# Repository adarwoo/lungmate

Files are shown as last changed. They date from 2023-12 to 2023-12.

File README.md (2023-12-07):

# Dust Extractor Manager for woodworking machinary

Guillaume Arreckx (United Kingdom)

**This was automatically translated from French**

This project should delight carpentry workshop owners who use
woodworking machinary with a chip dust extractor. Thanks to the
'LungMate', you no longer need to worry about the dust extractor,
because it turns on automatically each time you start one of the
machines in the workshop, then turns off once the work is finished. The
assembly is discreet and is placed directly in the workshop's electrical
panel. It precisely measures machine currents via a contactless Hall
effect sensor and transmits the results over a serial interface. It also
allows you to control the dust extractor manually with a simple push
button.

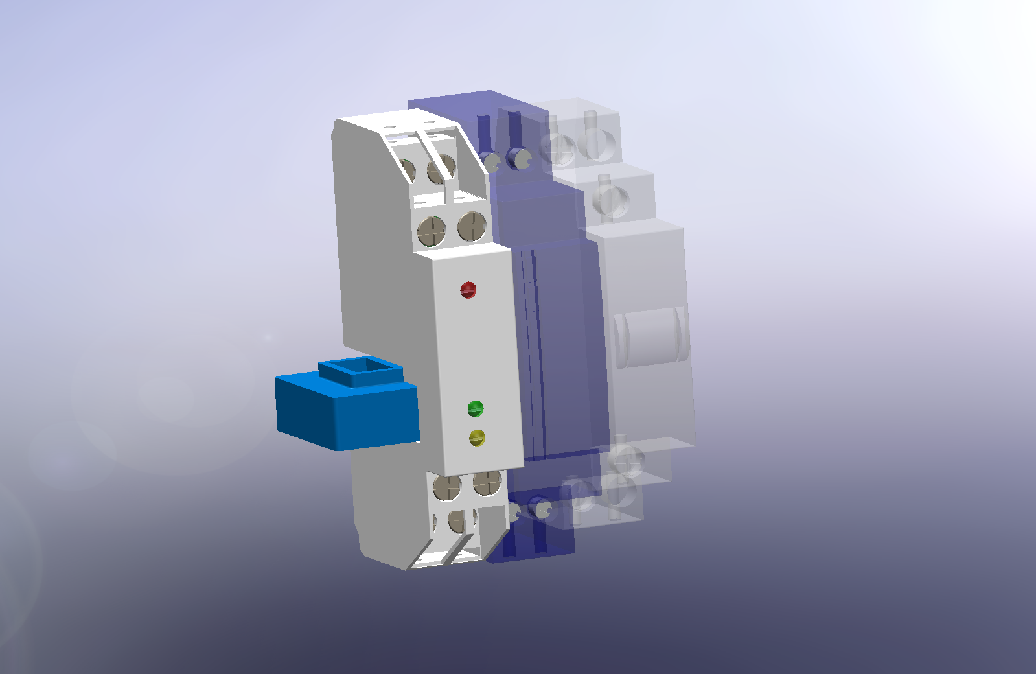
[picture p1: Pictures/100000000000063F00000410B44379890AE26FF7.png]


Woodworking machines generate enormous quantities of sawdust and the use
of a chip dust extractor is essential in a workshop. The paradox is that
these dust extractors generate a lot of fine and harmful dust in the
air. They are also noisy and power hungry. They should therefore only be
turned on when necessary. LungMate turns on the chip vacuum each time
one of the woodworking machines starts, then turns it off a few seconds
after the last machine stops, to allow the evacuation of the chips
remaining in the pipes.

Ignition is also slightly delayed; Woodworking machines, which mostly
use induction motors, require a very high starting current.

This delay avoids accumulating the starting currents of the woodworking
machine and the dust extractor, and can thus avoid blowing the pellets!

This implementation is low voltage only and uses a contactless Hall type
current sensor. The power supply and the relay which controls the dust
extractor use standard commercial modules. Ultimately, this achievement
finds its place in a box with the dimensions of the standard circuit
breakers found in modern electrical panels with a 35MM DIN rail. This
assembly is only intended for single-phase machines.

LungMate is also equipped with an RS232 type serial port, which allows
you to configure the module. Incidentally, all power measurements made
are transmitted 5 times per second. Connected to an external system,
this could, for example, make it possible to calculate the cost of the
electricity used...

-   # Plan



Figure 1. LungMate circuit

The assembly is structured around an AVR microcontroller from ATMEL, the
ATtiny861 which operates as conductor. This version of AVR is perfectly
suited for the type of measurement that we carry out here, in particular
thanks to its analog/digital converter which offers a differential mode
and a programmable gain input preamplifier, very useful here.

An external 8.192MHz crystal controls the AVR's internal clock. This
allows precise measurements without having to calibrate the AVR's
internal clock.

A small, standard male HE6 connector allows the microcontroller's flash
memory to be programmed using an SPI programmer for AVRs.
Spindle$$\overline{\text{RESET}}$$is also wired and allows the
connection of Atmel JTAG-ICE or Dragon emulators.

-   # Electronics in detail

Power supply is entrusted to an external module from Lambda, the DSP
10-12.

This switching module is the size of a standard circuit breaker and can
also be mounted on the 35mm rail of the electrical panel.

It provides up to 830mA of continuous and regulated 12V. This is way
more than we need.

The 12V voltage is necessary to drive the external monostable relay.

A small LDO type linear regulator lowers this voltage to 5V to power the
microcontroller and the analog part. This also benefits from additional
filtering by a small RC filter, while the power supply to the
analog/digital converter of the microcontroller is done by a suppression
choke to try to eliminate part of the internal digital noise.

The 3 LEDs are driven directly from 12V using small transistors to avoid
any fluctuation in the 5V power line and distort the measurements.
Ultimately, the current required on the 5V line is very low, with the
majority going to the current sensor.

Control of the dust extractor is entrusted here to a monostable modular
relay from the Italian company Finder. This relay has the following
advantages:

-   A format compatible with electrical panels with 35mm DIN rail
-   A continuous excitation voltage of 12V, with a 115ohm coil
-   A possible charge of 20A

The microcontroller drives it via a Darlington type transistor which
also powers the yellow signaling LED. A diode suppresses the feedback
from the relay coil.

The measured power range is vast! In order to determine when to turn on
the dust extractor, currents of a few hundred mA must be detected. A
small hand sander, for example, may only consume a few tens of Watts,
while at the other extreme, a workshop plane may use several tens of KW,
especially when starting up.

In addition, the module must be able to carry out reliable measurements
if these were to be used at the output of the serial interface.

The Hall sensor from LEM can measure currents up to 150A! With an
optimal range of 50A. The main advantage of this type of sensor is that
the output voltage is proportional and linear to the current passing
through it, with little variation linked to temperature.

The sensor output signal is biased to mid-rail of the power supply. A
small operational amplifier takes this signal and applies a 3rd order
analog anti-overlap filter to it before driving the AVR A/D converter
input. The bias voltage also attacks the microcontroller, which
internally differentiates the two voltages, then amplifies this
difference 8 times.

A few transistors are used here as an RS232 driver, rather than using an
integrated circuit, like the classic MAX232. The RS232 interface uses
±12V signals, although in practice we can be satisfied with ±5V, or even
0-5V over short distances. Here we use a trick, based on the fact that
the exchanges on the port are done alternately, recycling the negative
voltage from the input pin to the output. So only 2 transistors are
needed.

-   # Use

The module can be controlled by 1 or more push buttons to be placed
strategically in the workshop. A closed contact type button, with or
without integrated LED, does the trick. This allows, among other things,
to trigger the dust extractor manually.

In my workshop, the push button is mounted in the chute, next to the end
point of the suction pipe. The LED on the switch reminds you of the
current mode.

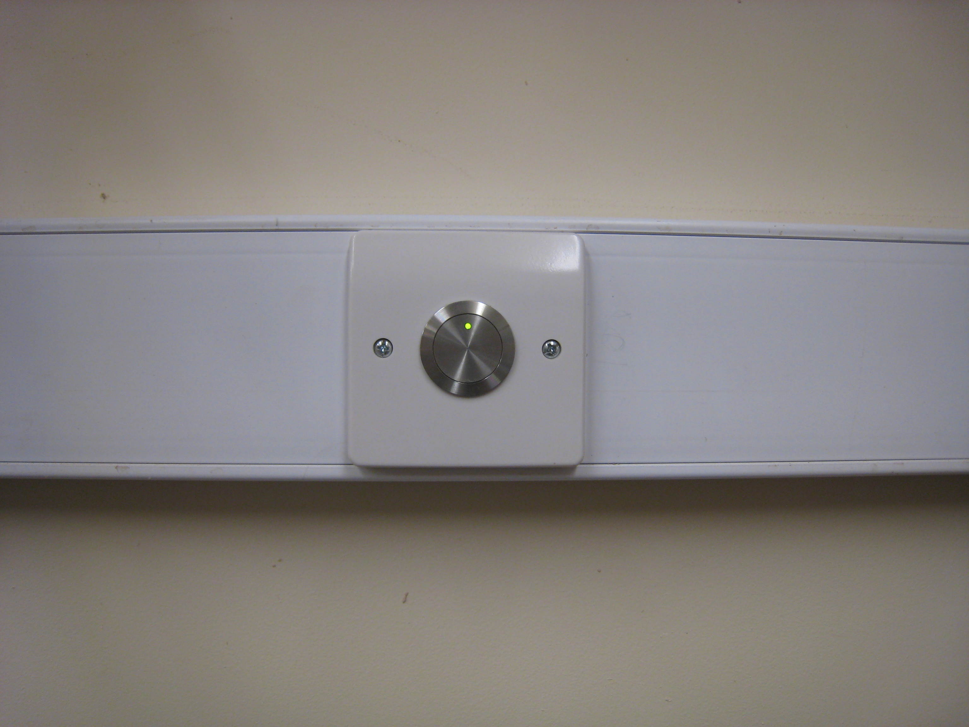
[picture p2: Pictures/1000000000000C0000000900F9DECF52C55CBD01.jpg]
The 3 modes are:

1.  AutoThe dust extractor turns on automaticallyThe LED flashes
2.  OnThe dust extractor is onThe LED is on
3.  OffThe dust extractor is offThe LED is off

Figure 2. Mode control button mounted in workshop chute

By default, upon power-up, the mode is Auto.

Depending on whether you press briefly or long, the mode changes
differently:

-   # The software

The software is almost entirely written in C and compiled with the free
tools of the WinAVR suite.

It has several parts:

1.  The main loop, which processes all real-time events, and calculates
    the apparent power.
2.  The machine state which controls remote control and LEDs
3.  The serial console, to change internal parameters, stored in the
    EEPROM

There are several methods of measuring an AC signal. Books on digital
signal processing are full of algorithms of all kinds!

Let us cite, among others, the algorithms of DFT (Discrete Fourier
Transform), FFT (Fast Fourier Transform), and the Goerzel algorithm.

It is also possible to rectify the 50Hz sinusoid using more electronics
and carry out a continuous measurement.

In the end, and despite the use of a small 8-bit microcontroller, the
solution chosen is the fast Fourier transform (FFT) algorithm. The
Fourier transform is an algorithm for converting a time signal into its
different frequency components, the amplitude of which can then be
measured.

This type of algorithm is often used by DSPs, processors specialized in
digital processing and which have specialized instructions for this type
of calculations.

The signal that we are measuring here is relatively slow (50Hz), and
moreover, we are only trying to measure one frequency of the spectrum –
50Hz. All this helps reduce the number of calculations (of Radix-2
Butterfly) and the AVR ultimately achieves this without any problem.

The FFT uses a window of 64 samples with sampling frequency such that
each frequency component or 'bin' has a width of 5Hz. This choice allows
us to measure frequencies of 50Hz or 60Hz (US) without the need for a
Windowing function, such as Hamming.

Each measurement is triggered by an interruption of the AVR's internal
Timer. A burst of 16 conversions into 10-bits is carried out by the ADC
in as short a time as possible.

The microcontroller is in Sleep mode at this time, which reduces
internal noise and improves analog measurement.

These 16 measurements are decimated to ultimately obtain a consolidated
12-bit measurement.

Each new consolidated measurement gives rise to a partial calculation
(1/64th) of the FFT.

At the 64th measurement, the final power is calculated and a new cycle
starts.

In the end, we obtain 5 new results per second. Each result is evaluated
by the automaton which controls the relay and the LEDs, then is
transmitted over the serial link.

The program, once compiled, fills practically the entire 8KB FLASH
memory. The 512 byte RAM is consumed 2/3 just by the FFT buffer.

As for the EEPROM, it stores the configuration parameters which can be
adjusted by connecting the module to a PC via its serial interface.

The AVR watchdog and BOD are continuously activated by setting the AVR
fuses to ensure proper operation. The Watchdog counter is reset to zero
in the main loop so that a hypothetical crash restarts the module. The
'Brown Out Detector' forces a reset if the voltage drops below 4.3V.

-   # The realization

The printed circuit is double-sided with 0.6mm metallized holes, which
are very difficult to produce at home. Another small problem, the
thickness of the IC must not exceed 1.2mm, otherwise, it will not fit
into the notches of the case. I tried with classic FR4 1.6mm, but
nothing, it doesn't work! On the other hand, the FR4 in 1.0mm is very
suitable.

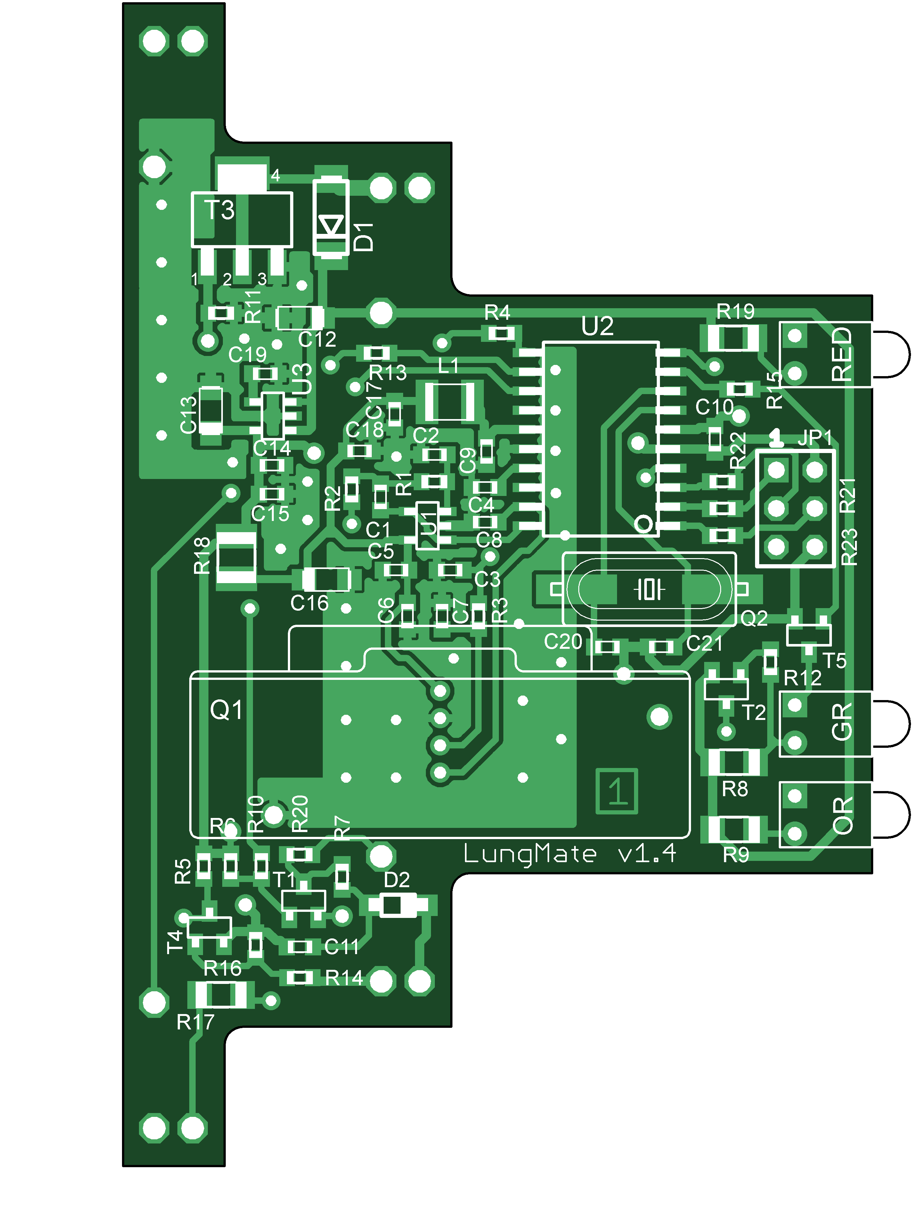
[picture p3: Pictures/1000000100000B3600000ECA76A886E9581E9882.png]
Soldering the components should
not pose too many difficulties for those who are used to soldering SMTs.
You should not be impressed by the small size of the 0603 boxes, they
can be soldered with a conventional iron (small soldering iron required)
or with reflux for the best equipped.

You absolutely need fine tweezers (forget mother-in-law's tweezers!), a
magnifying glass and skillful hands.

The soldering iron method must be accompanied by an additional supply of
flux during welding. Use a flux suitable for CMS, and clean up any
traces at the end - the job looks cleaner on the one hand, and on the
other hand, some fluxes can turn out to be corrosive in the long run.

Figure 3. The circuit with its SMD components

The 0603 packages must be soldered first, followed by the SOT23
transistors, and finally all the SMT components of the flattest or
thickest. Soldering the LEDs and the small connector is done just before
soldering the connection terminals.

The sensor can then be soldered, either directly on the IC, or by
raising it a little with a scrap of FR4 or any other insulator of
approximately 1.5mm thick to align the sensor hole with the face of the
case.

The box connection terminals are soldered directly to the printed
circuit. Everything slides into the grooves in the case provided for
this purpose. You need to drill 3 3mm holes on the front of the box to
pass the LEDs through, and cut out one of the blanks for the sensor. The
workshop's column drill is ideal for drilling the 3 holes. You can use
your gauge to mark the side cut, then make a first rough cut. The final
cut can be made with a cutter along the line of the gauge, because the
wall is relatively thin, but be careful with your fingers!

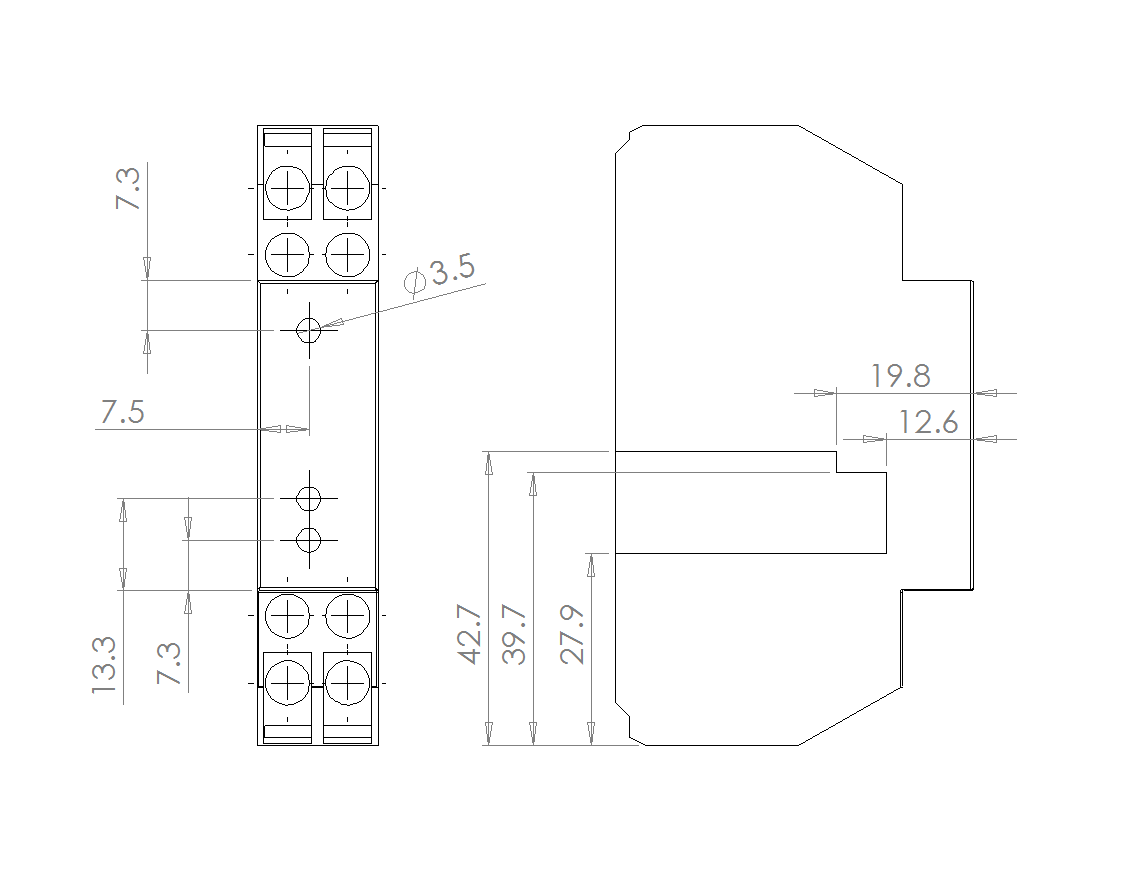
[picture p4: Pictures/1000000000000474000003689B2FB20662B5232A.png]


Figure 4. Cutout required for the box

-   # 

-   # Installation and connections

The LungMate, relay and power supply simply clip onto the panel rail.

But before any final assembly in the table, it is advisable to identify
all the pads of the module, even if it means using a felt-tip pen or a
label maker to mark each pad beforehand.

You must, of course, turn off the power before doing anything on the
board. None of the wires connected to the control module must be 230V –
that would be prohibitive! To facilitate this task, colored wires (other
than the colors already used in the table) with a diameter of 1mm can be
used for all low voltage connections.

For the system to function
correctly, the HAIS sensor must detect the current of all the machines
under monitoring. On the other hand, it should definitely not detect the
current of the dust extractor. Indeed, in automatic mode, once the
woodworking machine is turned off, the current sensor would continue to
detect the load of the dust extractor, and therefore would never turn
off!

In other words, we cannot simply pass the main incoming mains voltage
through the sensor. Detection works just as well with phases as with
neutrals – but especially not both or any mixture, otherwise we would
have made a differential!

Figure 5. Module wiring. All wires are low voltage.

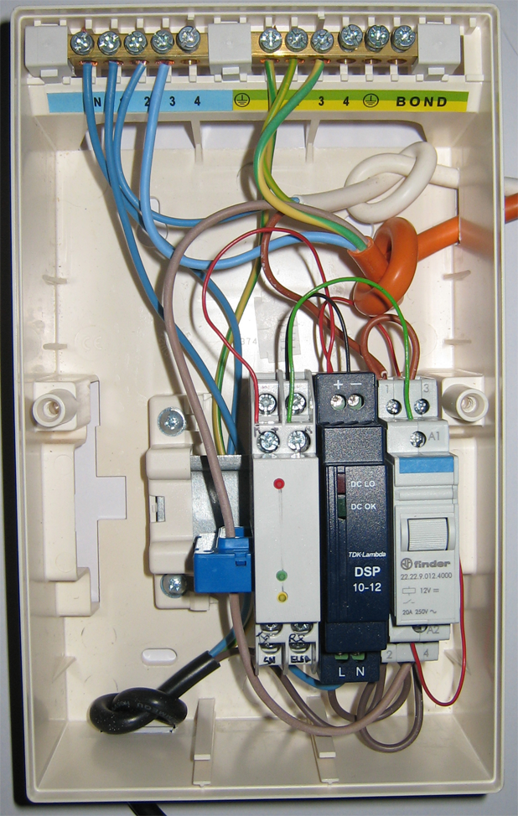
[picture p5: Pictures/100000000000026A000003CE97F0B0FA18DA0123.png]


Figure 6. Example of installation in a dedicated panel. Here only one
phase is used.

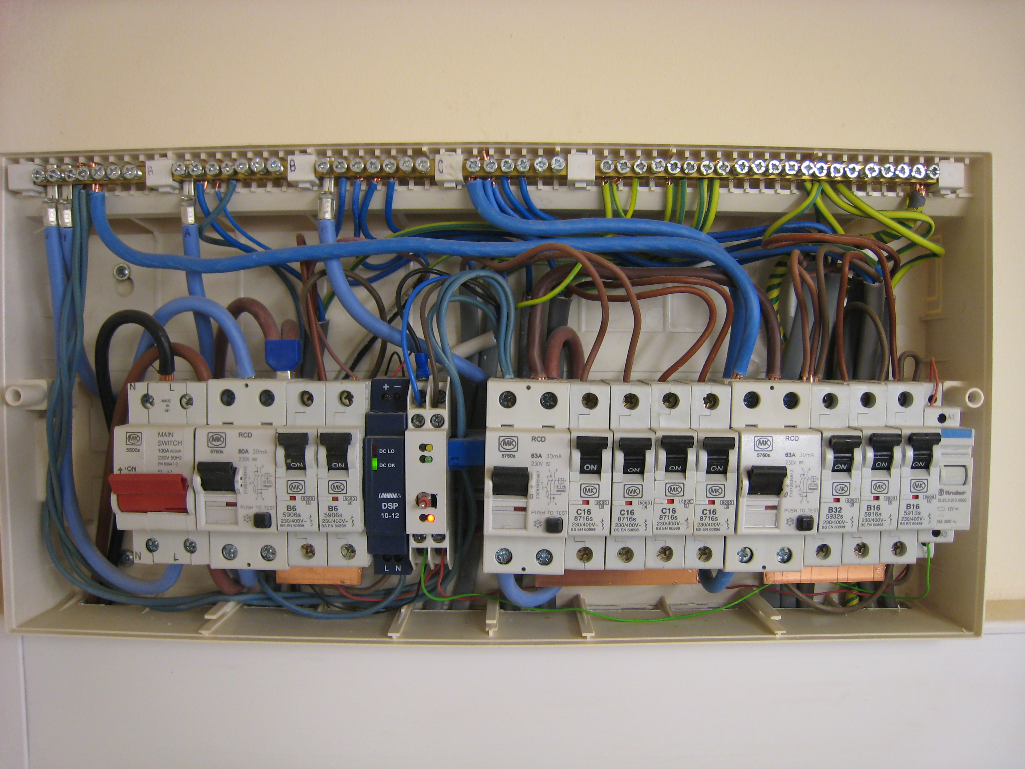
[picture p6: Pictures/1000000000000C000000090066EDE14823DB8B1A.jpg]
Figure 7. Example of
installation in a complete table exists. All machines are protected by a
differential block whose neutral return passes through the sensor. The
dust extractor is located on another differential block.

Only machines that you want to trigger suction must have one of their
power supply wires passed through the HAIS sensor. If only one machine
is managed, the phase wire can be passed through the sensor hole. If you
want to manage several machines at the same time, you must pass each
phase of each machine through the sensor. A better solution in this case
consists of grouping all the woodworking machines on a common
differential circuit breaker, and passing the neutral return of this
through the sensor.

Here is the layout diagram of my workshop, which is equipped with 5
power machines controlling the suction. All electrical circuits are
protected by differential circuit breakers, including the control module
and the dust extractor.

Figure 8. A workshop panel
wiring diagram will help an electrician find his way.

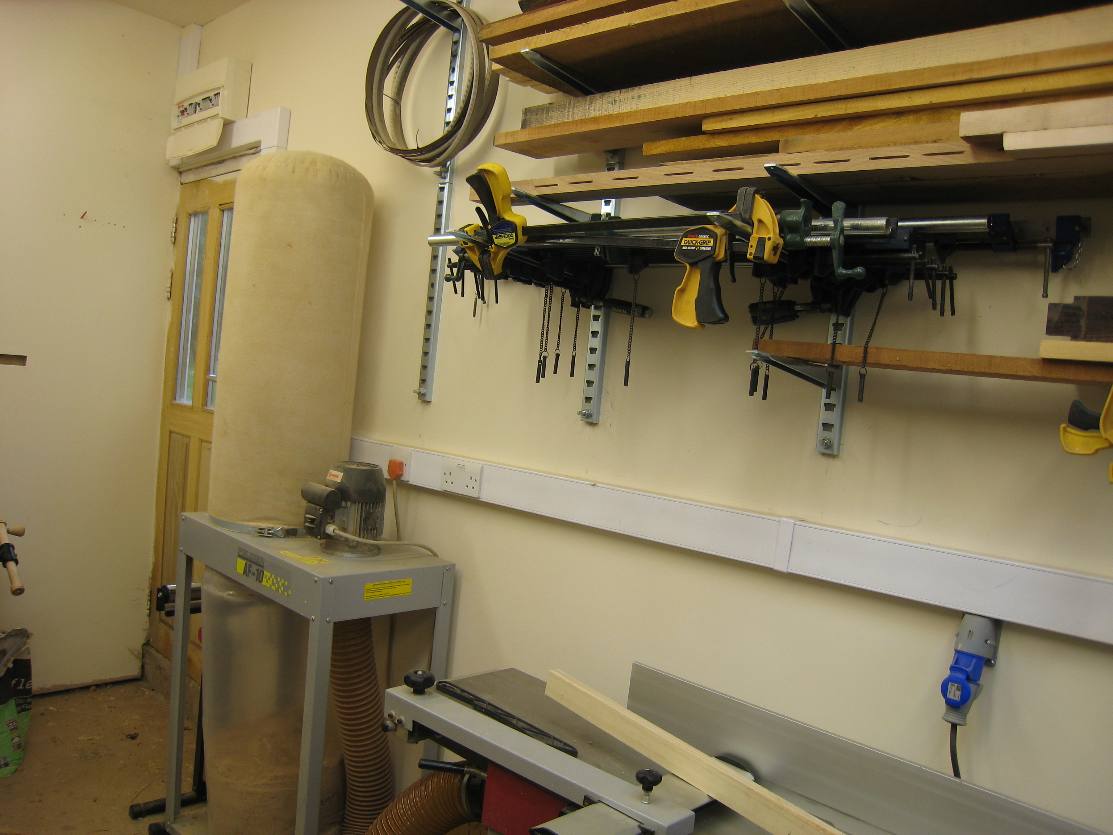
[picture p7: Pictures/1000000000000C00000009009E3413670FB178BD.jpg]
Figure 8. The electrical panel
in the workshop with the chip dust extractor.

-   # Module configuration

The module is pre-programmed with a number of standard parameters.

When powered up for the first time, the program reads the EEPROM memory
and calculates a 'checksum'. As this is incorrect, all default
parameters are then written to the EEPROM memory. At the next power-up,
only the EEPROM is valid.

Parameters can be changed by connecting the serial interface of the
module to a PC using any terminal emulator such as HyperTerminal.

Transmission is carried out in 8N1 at 19200 bauds (8Bits, 1 stop bit, no
parity) and no flow control.

Simply press \<Enter\> to activate console mode. In this mode, the
module does not carry out measurements.

| | | | | |
|---|---|---|---|---|
| Index | Description | Unit | Type of values | Default value |
| 1 | Power threshold required to trigger suction | Watt | From 50 to 9999 | 50 (Watt) |
| 2 | Restart in 'Auto' mode | \- | 0 for no1 for yes | 1 (yes) |
| 3 | Suction maintenance time once the load has disappeared | Second | From 0 to 99 | 5 (seconds) |
| 4 | Calibration coefficient | \- | From 1 to 32768 | 3380 |
| 5 | Central frequency to measure | Hz | From 40 to 70 | 50 (Hz) |

*Figure 9. Summary of configurable parameters in the console*

To change a value, you must enter the index of the value to modify then
\<Enter\>, followed by the new value.

Only valid characters are accepted. An error message is displayed if the
new value is out of norm. The message 'OK' indicates that the new value
has already been programmed.

A '0' exits console mode for measurement mode, and the system then
becomes active again.

If after 8 seconds nothing is typed, the watchdog restarts the module.

-   # List of components

**Resistors (all 0603, unless noted):**

R1 = 42k2 (1%)

R2 = 47k5 (1%)

R3 = 29k4 (1%)

R4, R20, R21, R22, R23 = 270Ω

R5, R10, R12, R13, R14, R15 = 10kΩ

R6, R11, R16 = 100kΩ

R7 = 4k7

R8, R9, R17, R19 = 680Ω (1206 housing)

R18 = 10Ω (1210 case)

**Capacitors (all 0603):**

C10 = 1 - 4.7µF (6.3V minimum)

C7, C19 = 4n7

C2 = 10nF

C20, C21 = 18pF

C4, C6, C8 = 47nF

C3 = 68nF

C1, C5, C9, C11, C14, C17 = 100nF

C15, C18 = 100pF

**Tantalum capacitors:**

C12, C13, C16 = 2µ2 in case A (16V)

**Semiconductors:**

U1 = MCP6001(T) Op-amp in SOT23-5 package or equivalent

U2 = Atmel Attiny861 20SU, SO20 case

U3 = Micrel MIC5205U or compatible

T1,T2 = BC857C

T4,T5 = BC848C

T3 = FZTA14

D1 = GF1A (DO214A)

D2 = BAT54 (SOD123)

LED1 = Red H13X type LED

LED2 = LED type H13X orange

LED3 = Green H13X type LED

**Miscellaneous:**

L1 = 10µH, in 1210 package, such as Murata LQH32CN100K

Q1 = HAIS-50P current sensor from HAIS (Farnell or RS)

Q2 = Quartz 8.192MHz in HC49 case

Relay, Finder 22.21.9.012.4000 (Farnell, 1765071)

Power module, Lambda DSP10-12

Housing, Altech 91.201 (RS, 2508420317)

JP1 = 2x3 pin connector with 2.54mm pitch

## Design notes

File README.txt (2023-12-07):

Project lungmate

Author: software@arreckx.com
==============================================================================

This directory contains the source files and CAD files for the lungmate
 project.
Lungmate is an electronic device, housed in a circuit breaker like case which
 controls the dust extractor of a woodworking workshop.

The detail documentation is not available from this project as it is my
 intention to publish it in Elektor magazine.

You will find, however, all of the data such as the software and the PCB files.

The PCB data was created using Eagle (www.cadsoft.de) version 5.6 and the PCB
 was built by PCB-POOL services.

The software was compiled using the winavr software suite under Windows.
It should possible to build it under Linux with no changes, including some
 of the simulation builds.

Software requirement for Windows build
--------------------------------------
Cygwin 1.6 or later. (Note not tested under 1.7.1). 
	Make sure to install gcc, mintty, python and make.
WinAvr 2009-03-13 or later from http://sourceforge.net/projects/winavr
Doxygen and graphviz for the documentation
AVRStudio can be used too.

Building the software
---------------------
The software should be built from a shell. In Cygwin, mintty is a good choice.
To build the lungmate software type:
make NDEBUG=1

The final build product can be found in dist/lungmate_release.hex
and should include the fuse and lock bits data too.

To build the unit tests, type:
make test

To build the simulation:
make sim

To build all:
make all

To find the list of all the targets:
make list

To build the code documentation using Doxygen:
make doc

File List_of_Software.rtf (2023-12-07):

List of soft

uTorrent - In download
Acrobat Reader - Get
Flash Player - Get
AVRStudio 4 - In downloade
Eagle - In download
Edimax Wireless LAN - Not required ?
eMule - Download
Java - Download with NetBeans
Logitech SetPoint - In download
Steam + MS Games Live + VC2005
Google Chrome - Download
OpenOffice 3.0 - CD ?
Perfect Disk 10 - in download
Quick Time alternative ?
Skype - download
Solidworks
TigthVNC
VirtualCloneDrive
WinAVR
WinRAR CD
Cygwin

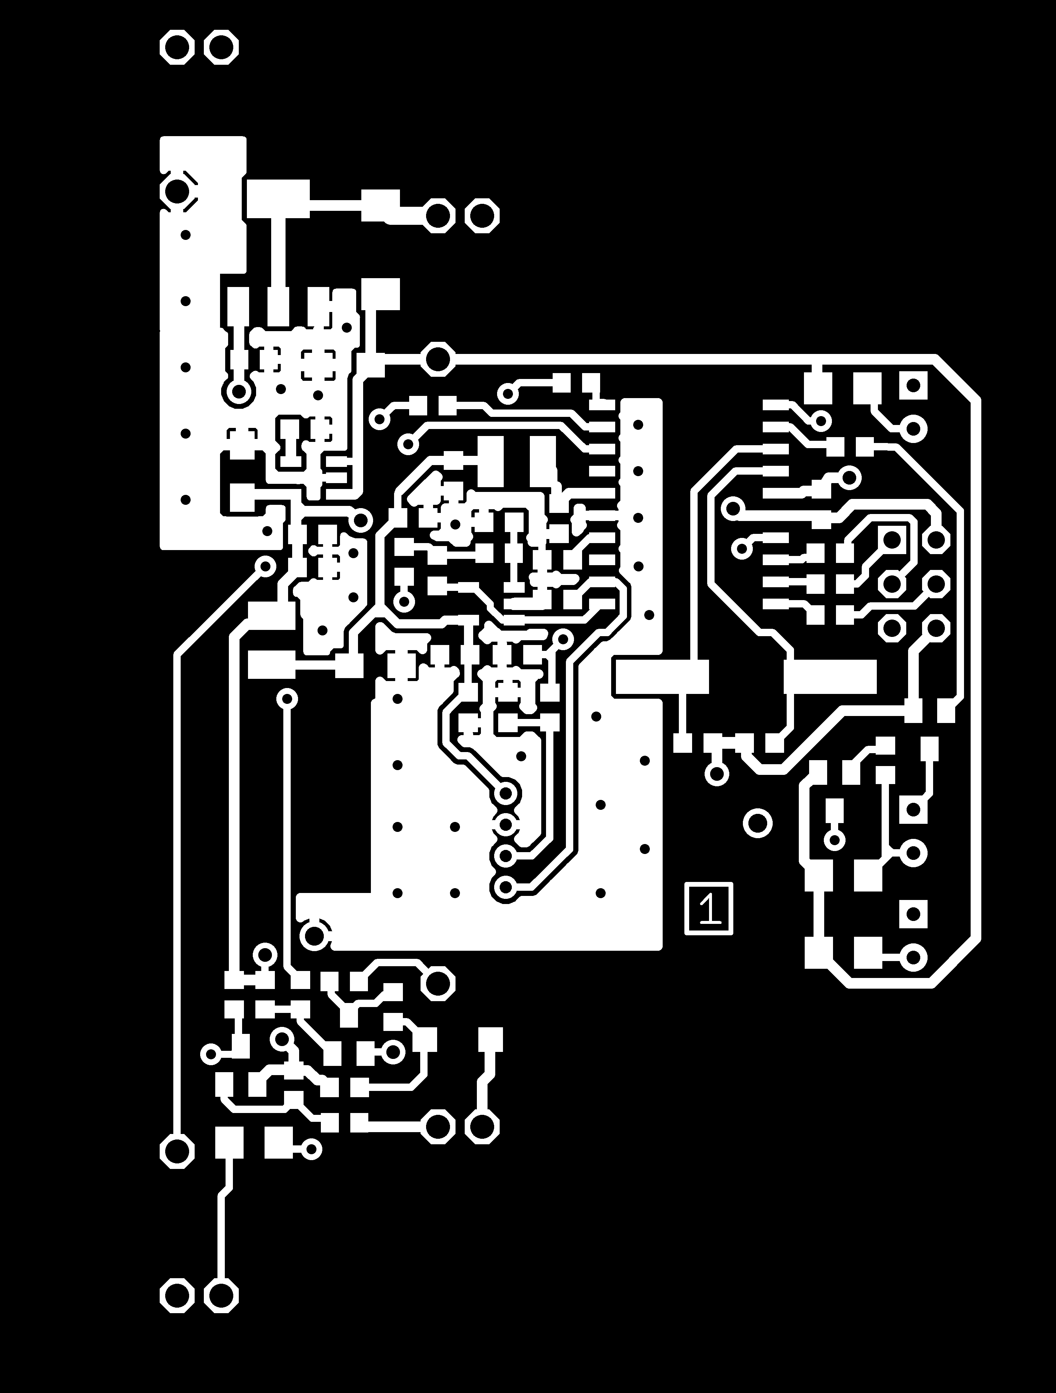
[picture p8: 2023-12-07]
docs/cad/PCB Top.png

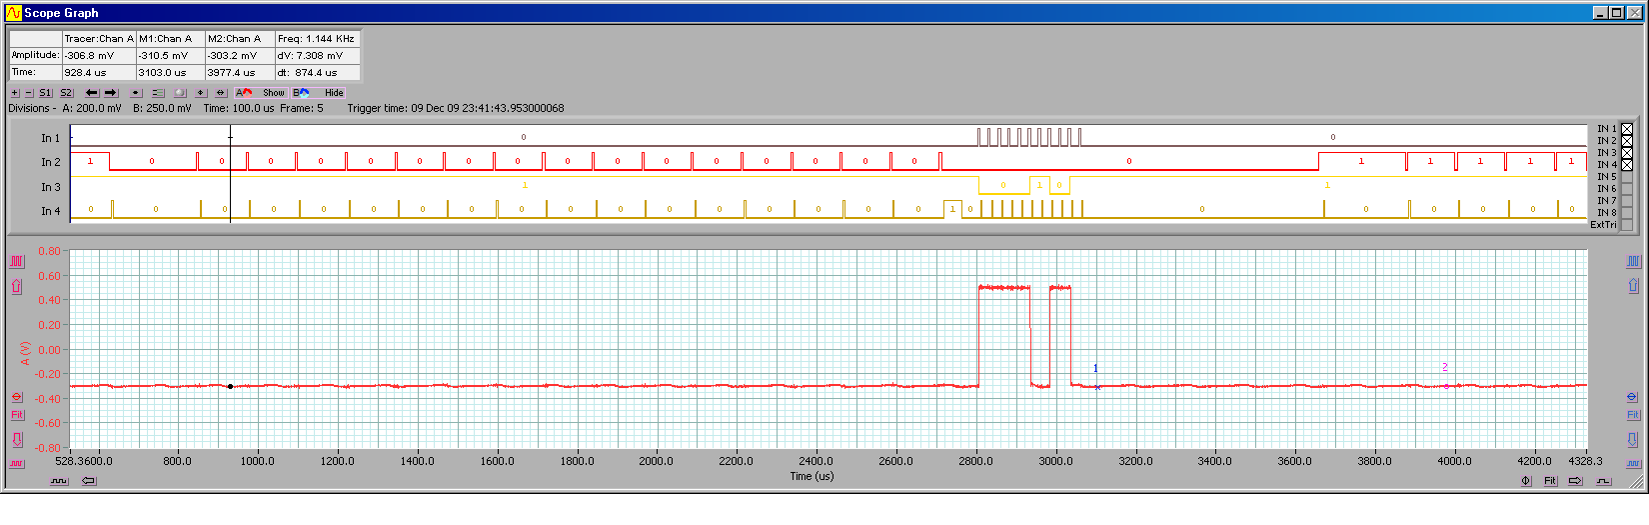
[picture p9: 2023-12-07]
docs/captures/main flow.PNG

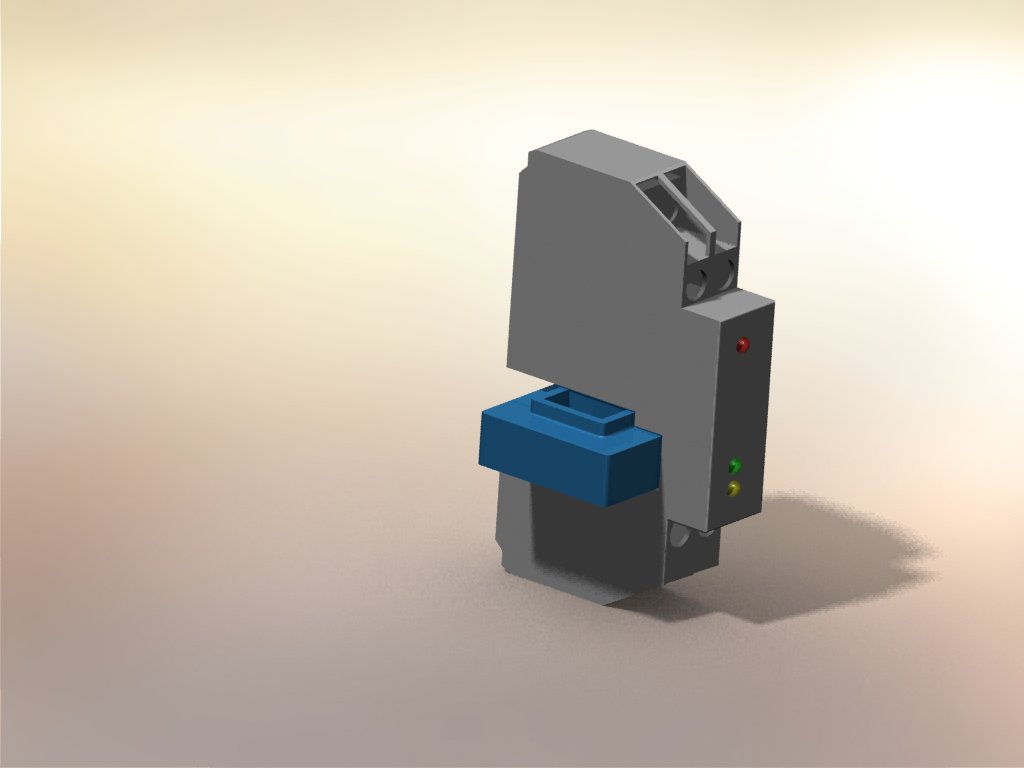
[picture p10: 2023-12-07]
lunmate_render.jpg

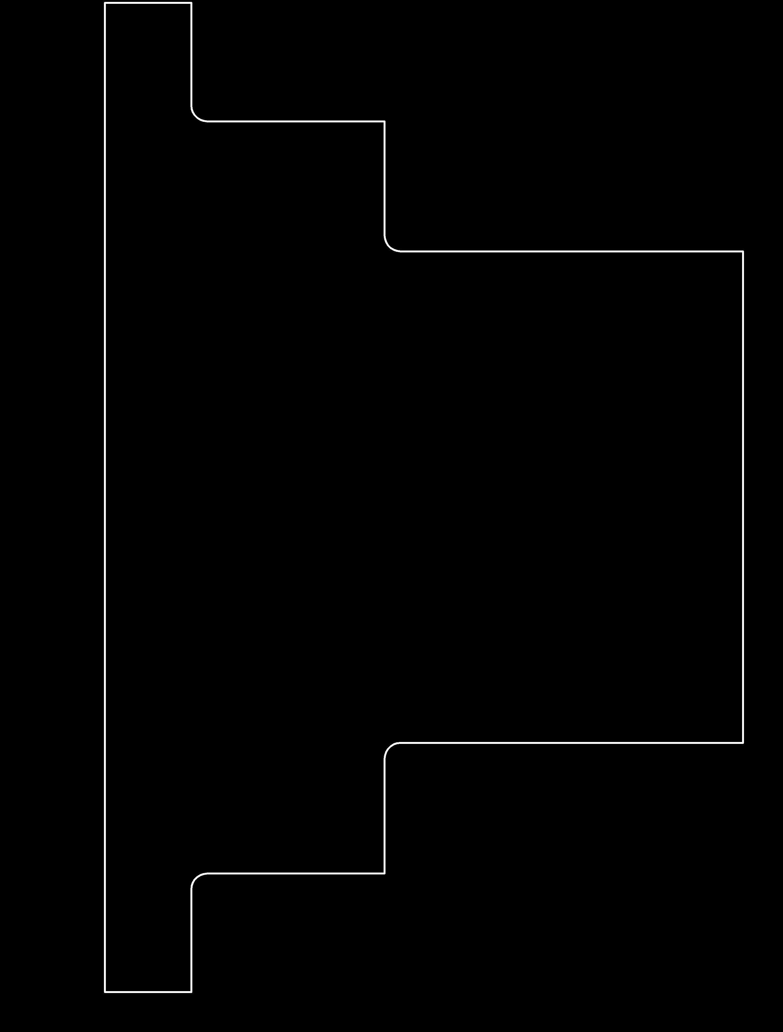
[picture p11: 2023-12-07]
docs/cad/PCB Outline.png

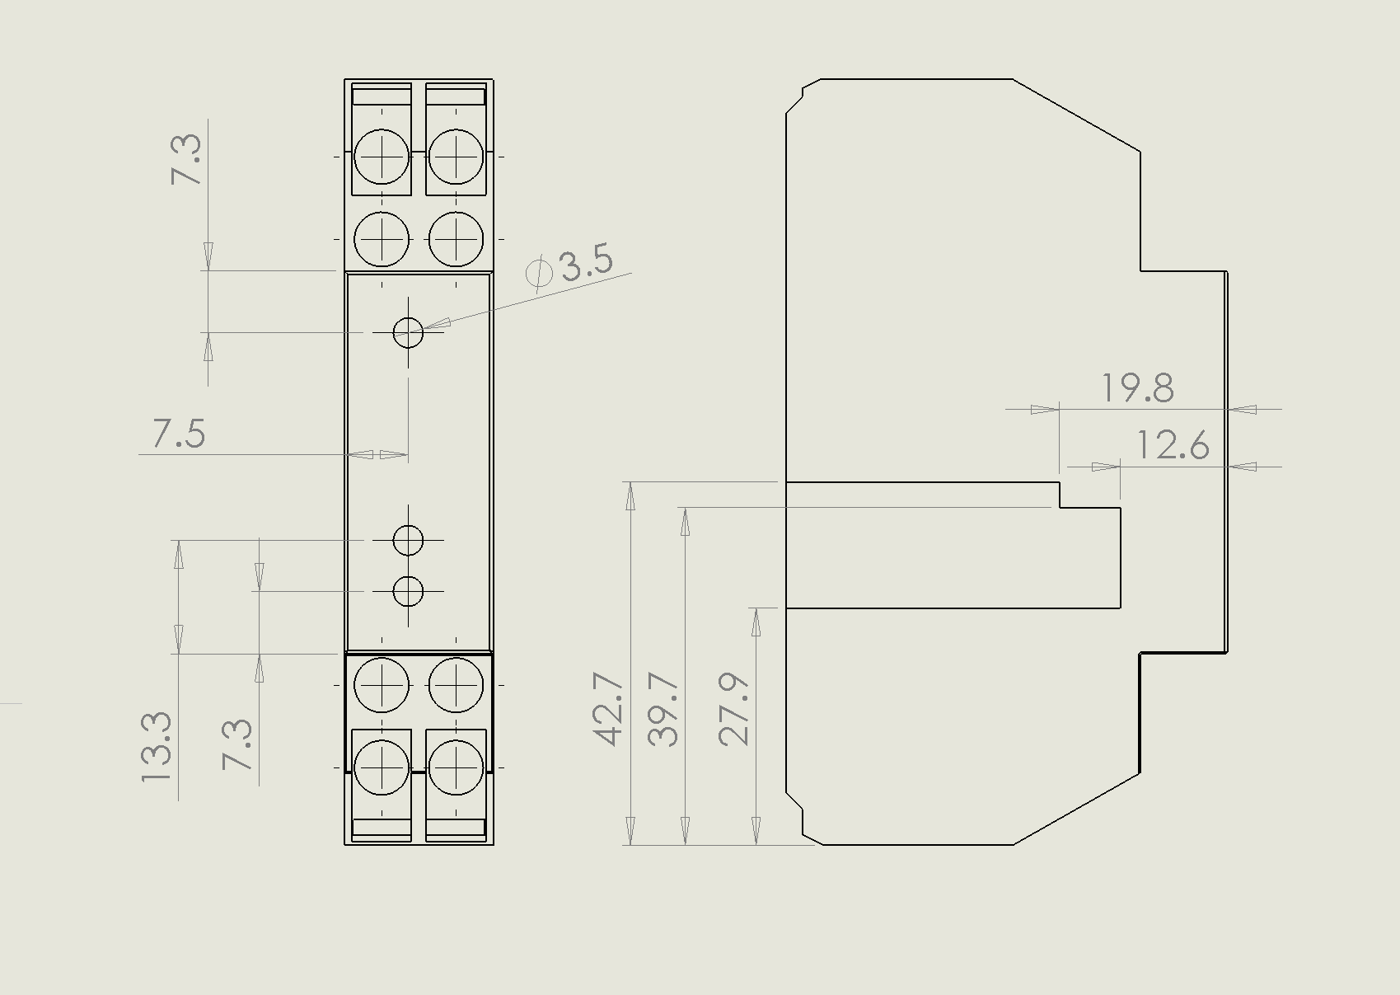
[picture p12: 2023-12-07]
cutout.PNG

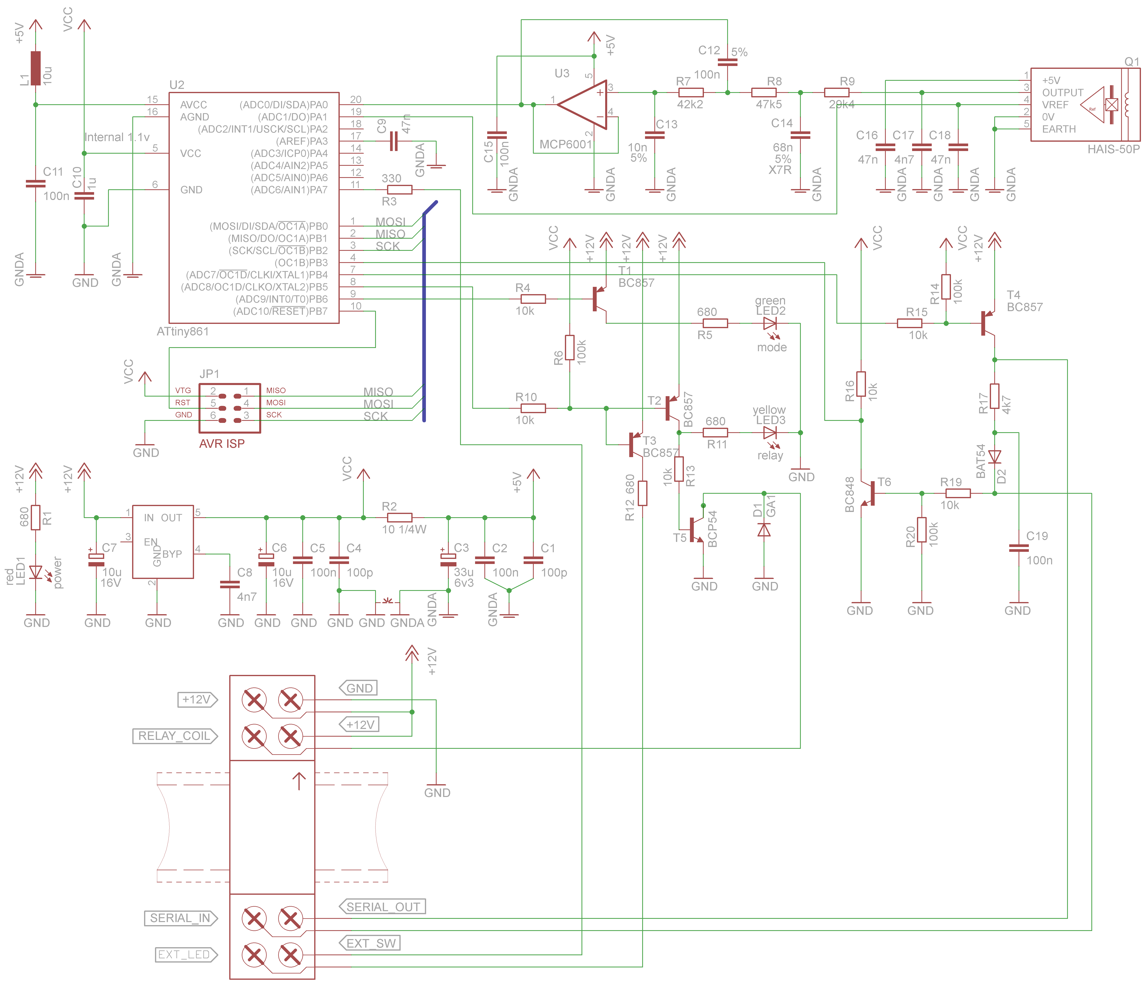
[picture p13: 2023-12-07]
dusmate_sch.png

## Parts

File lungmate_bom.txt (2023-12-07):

Partlist exported from C:/Users/gpa/Documents/dev/lungmate/eagle/lungmate.sch at 26/01/2010 20:32:36

Qty Value     Device               Parts                      
1   1u        C-EUC0603K           C10                        
3   2u2       CPOL-EUSMCA          C12, C13, C16              
1   4k7       R-EU_R0603           R7                         
2   4n7       C-EUC0603K           C7, C19                    
1   8.192MHz  CRYSTALHC49UP        Q2                         
1   10 1/4W   R-EU_R1210           R18                        
6   10k       R-EU_R0603           R5, R10, R12, R13, R14, R15
1   10n       C-EUC0603K           C2                         
1   10u       L-EUL1210            L1                         
2   22p       C-EUC0603K           C20, C21                   
1   29k4      R-EU_R0603           R3                         
1   42k2      R-EU_R0603           R1                         
1   47k5      R-EU_R0603           R2                         
3   47n       C-EUC0603K           C4, C6, C8                 
1   68n       C-EUC0603K           C3                         
1   91.201S   91.201S              K2                         
3   100k      R-EU_R0603           R6, R11, R16               
6   100n      C-EUC0603K           C1, C5, C9, C11, C14, C17  
2   100p      C-EUC0603K           C15, C18                   
4   270       R-EU_R0603           R20, R21, R22, R23         
1   330       R-EU_R0603           R4                         
4   680       R-EU_R1206           R8, R9, R17, R19           
1   ATtiny861 ATTINY61TINY861-20SU U2                         
1   AVR-ISP-6 AVR-ISP-6            JP1                        
1   BAT54     DIODE-SOD123         D2                         
2   BC848     BC848                T4, T5                     
2   BC857C    BC857ALT1SMD         T1, T2                     
1   FZTA14    FZTA14               T3                         
1   GF1A      DIODE-DO214AA        D1                         
1   GND-GNDA  GND-GNDA             ~NUDEV~                    
1   GREEN     LEDH13X              LED1                       
1   HAIS-50P  HAIS                 Q1                         
1   MCP6001   OPA340N              U1                         
1   MIC5205U  MIC5205U             U3                         
1   ORANGE    LEDH13X              LED2                       
1   RED       LEDH13X              LED3

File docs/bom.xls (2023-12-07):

/Documents/dev/lungmate/eagle/lungmate.sch at 06/01/2010 11:20:29
Qty | Type | Manufacturer | Reference | Value | Case | Parts
6 | Capacitor |  |  | 100n | C0603 | C1, C5, C9, C11, C14, C17
1 | Capacitor |  |  | 1u | C0603 | C10
2 | Capacitor |  |  | 100p | C0603 | C15, C18
1 | Capacitor |  |  | 10n | C0603 | C2
2 | Capacitor |  |  | 22p | C0603 | C20, C21
1 | Capacitor |  |  | 68n | C0603 | C3
3 | Capacitor |  |  | 47n | C0603 | C4, C6, C8
2 | Capacitor |  |  | 4n7 | C0603 | C7, C19
1 | Inductor | Murata | LQH32CN100 | 10uH | L1210 | L1
1 | Crystal |  |  | 8.192MHz | HC49 | Q2
1 | Current Sensor | Hais | HAIS-50P |  | HAIS | Q1
1 | Diode |  |  | GF1A | DO214 | D1
1 | Diode |  |  | BAT54 | SOD123 | D2
1 | Enclosure | Altech |  | 91.201S | - | K2
1 | Header |  |  | AVR-ISP-6 | H6 | JP1
1 | Op-Amp | Microchip |  | MCP6001 | SOT23-5 | U1
1 | Led | MARL |  | YELLOW | LEDH13X | LED1
1 | Led | MARL |  | GREEN | LEDH13X | LED2
1 | Led | MARL |  | RED | LEDH13X | LED3
1 | Microcontroller | ATMEL |  | ATtiny861 | SO20 | U2
1 | LDO | Micrel |  | MIC5205U | SOT223 | U3
3 | Capacitor Tantalum |  |  | 2u2 | A | C12, C13, C16
1 | Resistor |  |  | 42k2 | R0603 | R1
1 | Resistor |  |  | 10 1/4W | R1210 | R18
1 | Resistor |  |  | 47k5 | R0603 | R2
4 | Resistor |  |  | 270 | R0603 | R20, R21, R22, R23
1 | Resistor |  |  | 29k4 | R0603 | R3
1 | Resistor |  |  | 330 | R0603 | R4
6 | Resistor |  |  | 10k | R0603 | R5, R10, R12, R13, R14, R15
3 | Resistor |  |  | 100k | R0603 | R6, R11, R16
1 | Resistor |  |  | 4k7 | R0603 | R7
4 | Resistor |  |  | 680 | R1206 | R8, R9, R17, R19
1 | Darlington NPN |  |  | BZPA14 | SOT223 | T3
3 | Transistor NPN |  |  | BC848 | SOT23 | T1, T4, T5
1 | Transistor PNP |  |  | BC857C | SOT23 | T2

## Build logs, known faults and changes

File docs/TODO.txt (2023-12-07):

Things left to do
-------------------------------------

1 - Is there a bug with the console when entering a number with many del etc..
2 - The serial port only works at 19200. Check offset value.
    Re-test with new board using a crysal

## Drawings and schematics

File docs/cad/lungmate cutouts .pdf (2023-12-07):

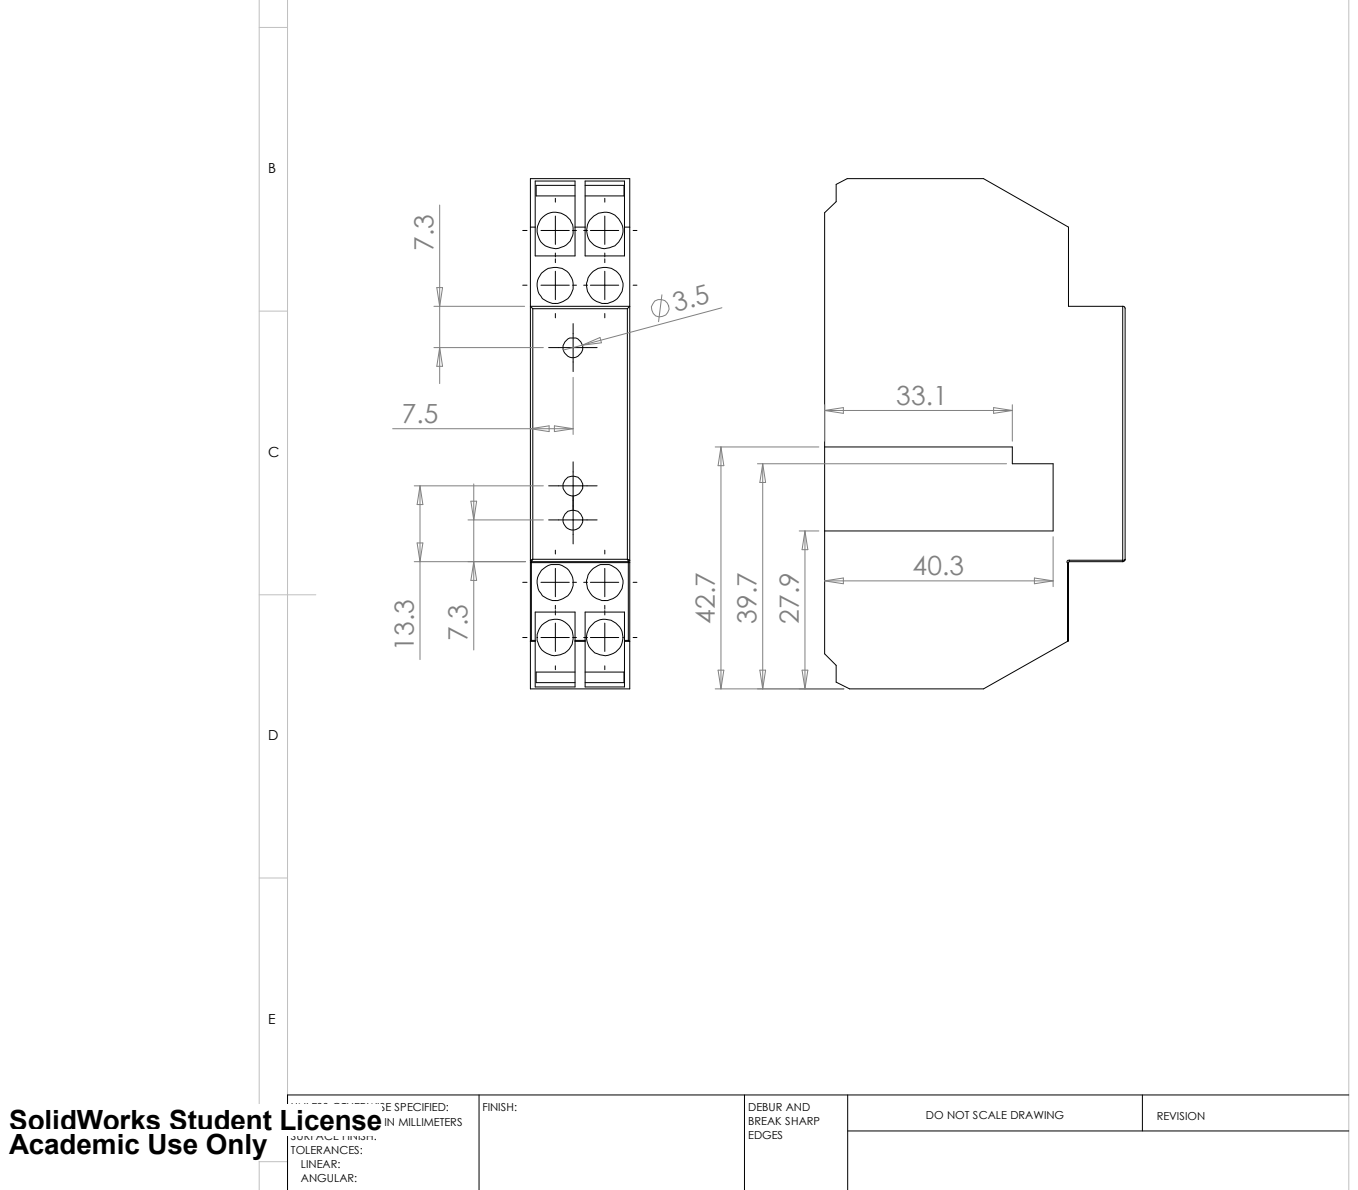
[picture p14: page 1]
DO NOT SCALE DRAWING; REVISION; EDGES; FINISH:; BREAK SHARP; DEBUR AND

SolidWorks Student License
Academic Use Only

UNLESS OTHERWISE SPECIFIED:
DIMENSIONS ARE IN MILLIMETERS
SURFACE FINISH:
TOLERANCES:
LINEAR:
ANGULAR:

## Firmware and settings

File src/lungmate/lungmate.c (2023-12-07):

/**@defgroup lungmate Lungmate Dust-Exctractor Controller*/
/**@ingroup lungmate*/
/**@file
 *****************************************************************************
 * Entry point, initialisation, and main loop for this application
 * @mainpage
 * <h1>Introduction</h1>
 * Lungmate application have been written to control the dustextractor of a
 *  workshop whenever a load is detected in the mains.
 * This application has been specifically written for a Atmel ATTiny861
 *  micro-controller chip, although most of the API could be easily ported and
 *  reused on other AVR micro-controllers.
 * <h1>Overview</h1>
 * This application is mostly interrupt driven.
 *
 * Only 4 interrupts are used:
 * <ul>
 * <li>The 'timer 1 overflow' is used to drive a burst of 16 conversions
 *  at 320 bursts/sec</li>
 * <li>The 'ADC conversion complete' is used to collect oversampled results,
 *  and to compute decimated values</li>
 * <li>A level change on the serial Rx pin will cause the system to enter</li>
 *  the terminal mode which allows all parameters to be changed</li>
 * <li>The 'timer 0 16-bits compare' is used to sample serial port bits</li>
 *  </ul>
 *  The timer 1 interrupt also services the keypad, which feeds into
 *  the state machine.
 *
 * The processing of decimated values by the FFT algorithm is handled in
 *  the main program.
 *
 * The real time arrangement is such that the computation of the FFT
 *  is finished well before the next timer interrupt.
 *
 * For each new FFT result (every 64samples - 200ms), the state machine
 *  is updated and the relay status re-evaluated.
 *
 * <h1>Getting started</h1>
 * Lungmate entry point is implemented in lungmate.c main function
 *  although the initialisation phase takes place in preamble() defined in preamble.c.
 * The A/D measurements take place in adc.c.
 * The state machine (stateMachine.c) is updated by the main loop.
 * <br/>The fft coefficient factor - or twiddle factors are created by a Python
 *  script placed in utils. The resulting file is twiddle.c and should be compiled
 *  the normal way.
 * Check the following sections for reference
 * @subpage lungmate
 * @subpage lib
 * @subpage unittest
 * @subpage simulation
 *
 * @author software@arreckx.com
 *****************************************************************************
 */

#include "wgx.h"
#include "fft.h"
#include "uart.h"
#include "console.h"
#include "dbg.h"
#include "stateMachine.h"
#include "adc.h"
#include "preamble.h"
#include "nvParam.h"
#include "key.h"


/** Mutltiplier for converting the FFT result into Watts */
static float fftToWatt;

/** Index of the next character to transmit (negative numbers to send carriage return etc.) */
static int8_t txCharIndex;

/** Stores the string value of the last know fft result (watt) */
static char acFFTResult[CONSOLE_MAX_CHARACTERS_IN_UINT16];


/**
 * Sends the fftResult down the serial link a character at a time
 *  to leave plenty of time before the next interrupt.
 * This happens after each partial fft computation.
 *
 * @return true if more characters remain to send
 */
static inline bool sendResult(void)
{
   bool retval = true;

   if ( txCharIndex >= 0 )
   {
      uartTransmit( acFFTResult[txCharIndex] );
      --txCharIndex;
   }
   else if ( txCharIndex == -1 )
   {
      uartTransmit('\n');
      --txCharIndex;
   }

   else if ( txCharIndex == -2 )
   {
      uartTransmit('\r');
      --txCharIndex;
   }
   else
   {
      retval = false;
   }

   return retval;
}


/** Process incomming traffic from the serial port */
static inline void enterConsole(void)
{
   // Read the character the incomming character
   int c = uartGetChar();

   // To enter the console mode, the first transmitted char
   //  should be a carriage return or linefeed
   if ( c == '\n' || c == '\r' )
   {
      // Finish transmitting the fft result
      while ( sendResult() )
      {
         continue;
      }

      // Enter console mode
      consolePrompt();
   }

   // Resume measurements and re-enable the interrupts that were
   //  disabled when a new character was received through a callback
   fftReset();
   adcInit();

   // Reset the index of the next char to send
   txCharIndex = INT8_MIN;
}


/** Process new adc value */
static inline void processAdcValue(void)
{
   // Compute part of the FFT and check whether this calculation has yeilded a new result
   if ( fftNext( adcGetValue() ) )
   {
      // Get the power from the FFT
      float result = fftGetResult() * fftToWatt;
      uint16_t fftResult = -1;

      // Clip at 65kw and pass to the state machine
      if ( result < 65535.0 )
      {
         // Cast to short
         fftResult = (uint16_t)result;
      }

      // Pass to the stateMachine
      smProcessFFTResult(fftResult);

      // Store the string representation in our text buffer to transmit later on
      for( txCharIndex=0; fftResult != 0 || txCharIndex == 0 ; ++txCharIndex, fftResult /= 10)
      {
         acFFTResult[txCharIndex] = (fftResult % 10) + '0';
      }

      // This is the best place to reset the watchdog
      // Reaching this point indicates all interrupts and computations
      //  are running fine. (every 200ms)
      wdt_reset();
   }
   else
   {
      sendResult();
   }
}


/**
 * Entry point of this application.
 *
 * @return 0 for ANSI compiance only. Should never ever return.
 */
int main(void)
{
   // Initialise all APIs
   preamble();

   // Read from eeprom the power conversion
   fftToWatt = nvParam( fftToWattRatio_e ) / 1000;

   // Enter the main loop where we wait for the decimation to have completed
   for (;;)
   {
      // Enter sleep. This may start an ADC conversion
      sleep_mode();

      // The debug pin will show (on an oscilloscope) the time taken to
      //  process the data in this loop. It will stay set in console mode.
      // This pin should clear before the next timer interrupt.
      dbgSet(DBG_MAIN_LOOP);

      if ( uartHasChar() ) // Is the serial port receiving a new character?
      {
         enterConsole();
      }
      else if ( adcTick() ) // Is the adc is about to start a new conversion batch?
      {
         smProcessTick();
      }
      else if ( adcHasNewValue() ) // Do we have a decimated value to process?
      {
         processAdcValue();
      }

      dbgClear(DBG_MAIN_LOOP);
   }

   // Unreachable !
   return 0;
}


/* ----------------------------  End of file  ---------------------------- */

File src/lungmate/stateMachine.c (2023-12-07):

/**
 *@ingroup lungmate
 *@{
 *@file
 *****************************************************************************
 * State machine controlling the action of the keypad and the state of
 *  the relay.
 * This state machine is also responsible for turning all LEDs on/off
 *
 * @author software@arreckx.com
 *****************************************************************************
 */

#include "wgx.h"
#include "nvParam.h"
#include "stateMachine.h"
#include "key.h"
#include "fft.h"
#include "adc.h"
#include "console.h"
#include "uart.h"

/** 
 * Size of the hysteris for the detection in Watt. This value 
 * means that a fluctation less than that size would not cause 
 * another detection 
 **/ 
static const uint8_t THRESHOLD_HYSTERISIS = 20;

/** Defines the required states for the relay */
typedef enum
{
   /** Relay is closed */
   smRelayOn_e,
   /** Relay is open */
   smRelayOff_e,
} smStatus_t;

/** Defines the current mode of operation */
typedef enum
{
   /** DE is off */
   smModeOff_e,
   /** DE is on */
   smModeOn_e,
   /** Auto mode for DE */
   smModeAuto_e
} smMode_t;

/** System timer tick of the time when it was off */
static uint32_t timeStamp;

/** Consecutive above the threshold */
static uint8_t countOn;

/** Consecutive below the threshold */
static uint8_t countOff;

/** Current status */
static smStatus_t status;

/** Current mode */
static smMode_t mode;

/** For the blinking */
static uint8_t blinkCycle;

/** Trigger off thresholds in Watts */
static uint16_t thresholdLow;

/** Trigger on thresholds in Watts */
static uint16_t thresholdHigh;

/** Keep relay on n * 200ms after the load has dropped */
static uint8_t countOffDeactivate;


/*-
 * Helpers for controlling the ports
 */

/** Turns the relay OFF. (Open the relay) */
static inline void relayOff(void)
   { RELAY_PORT &= ~_BV(RELAY_BIT); }

/** Turns the relay ON. (Close the relay) */
static inline void relayOn(void)
   { RELAY_PORT |= _BV(RELAY_BIT); }

/** Turn on both mode LEDs */
static inline void modeLedOn(void)
{
   MODE_LED_PORT |= _BV(MODE_LED_BIT);
}

/** Turn off both mode LEDs */
static inline void modeLedOff(void)
{
   MODE_LED_PORT &= ~ _BV(MODE_LED_BIT);
}

/** Alternate both mode LEDs */
static inline void modeLedToggle(void)
{
   MODE_LED_PORT ^= _BV(MODE_LED_BIT);
}


/**
 * Update the front LED to indicate the mode
 * This method is called just before the keypad, at regular
 * interval of 20ms.
 *
 * OFF  -> LED off
 * ON   -> LED on
 * AUTO -> LED flashing
 */
static void smUpdateModeLed(void)
{
   switch ( mode )
   {
   case smModeOff_e:
      // Turn off the LED
      modeLedOff();
      blinkCycle = 0;
      break;
   case smModeOn_e:
      // Turn ON the LED
      modeLedOn();
      blinkCycle = 0;
      break;
   case smModeAuto_e:
      // Flash fast - 4Hz, T=250ms, Half T=125ms
      // Alternate LED every 6 cycles
      if ( blinkCycle == 0 )
      {
         // New cycle - simply flip bit. That way, if on, it goes off, off it goes on
         modeLedToggle();
      }

      if ( ++blinkCycle > SM_MODE_BLINK_PERIOD )
      {
         blinkCycle = 0;
      }
      break;
   }
}


/**
 * Initialise the state machine and the front panel
 */
void smInit(void)
{
   // Prepare the relay port
   relayOff();
   DDR_OF(RELAY_PORT)  |= _BV(RELAY_BIT);

   // Prepare the mode indication LED
   modeLedOff();
   DDR_OF(MODE_LED_PORT) |= _BV(MODE_LED_BIT);

   // Initialise the mode from eeprom value
   if ( nvParam(restartInAutoMode_e) == 1 )
   {
      mode = smModeAuto_e;
   } 
   else
   {
      mode = smModeOff_e;
   }

   // Initialise the state machine internals
   status = smRelayOff_e;
   timeStamp = 0;
   countOn = 0;
   countOff = 0;
   blinkCycle = 0;

   // Triggering threshold given in Watts
   thresholdHigh = (uint16_t)nvParam(powerThreshold_e);

   // Compute some hysterisis to avoid excessive on/off cycles
   thresholdLow = thresholdHigh - THRESHOLD_HYSTERISIS;

   // Time to keep the relay on after the load has come off, expressed as 1/5th of seconds
   countOffDeactivate = (uint8_t)nvParam(keepOnAfter_e) * 5;
}


/**
 * Process a new value computed by the FFT
 *
 * @param value Measured power in Watt
 */
void smProcessFFTResult( uint16_t value )
{
   // Determine whether we should be on or off
   //  independently of the state we're in (on/off/auto)
   // This is to allow the system to come on instantanously when
   //  swithing between modes, and to avoid turning off when alternating
   //  between ON and AUTO.
   if ( status == smRelayOff_e && value >= thresholdHigh )
   {
      countOff = 0;

      if ( ++countOn > SM_COUNT_ON_ACTIVATE )
      {
         status = smRelayOn_e;
      }
   }

   if ( status == smRelayOn_e && value <= thresholdLow )
   {
      countOn = 0;

      if ( ++countOff > countOffDeactivate )
      {
         status = smRelayOff_e;
      }
   }

   // Given the mode we're in, toggle the relay.
   switch ( mode )
   {
   case smModeOn_e:
      relayOn();
      break;
   case smModeAuto_e:
      if ( status == smRelayOn_e )
      {
         relayOn();
      }
      else
      {
         relayOff();
      }
      break;
   default:
      relayOff();
   }
}


/**
 * Called by the key pad to indicate a single push was detected
 * Single push cycles the modes:
 *  OFF -> AUTO -> ON -> AUTO ...
 */
void smProcessLongKey(void)
{
   switch ( mode )
   {
   case smModeOff_e:
      mode = smModeAuto_e;
      break;
   case smModeOn_e:
      mode = smModeAuto_e;
      break;
   case smModeAuto_e:
      mode = smModeOn_e;
      break;
   }
}


/**
 * Called by the keypad to indicate a long push was detected. A
 * long push act to set the mode from its current. The mode
 * switches as follow:

 *  AUTO -> OFF  -> ON -> OFF
 */
void smProcessShortKey(void)
{
   switch ( mode )
   {
   case smModeOff_e:
      mode = smModeOn_e;
      break;
   case smModeOn_e:
      mode = smModeOff_e;
      break;
   case smModeAuto_e:
      mode = smModeOff_e;
      break;
   }
}
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
